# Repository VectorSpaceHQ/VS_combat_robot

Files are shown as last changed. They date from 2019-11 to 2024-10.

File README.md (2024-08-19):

This is an open source, low cost, DIY combat robot kit. It is designed for use with antweight (1lb) and beetleweight (3lb) combat robots.

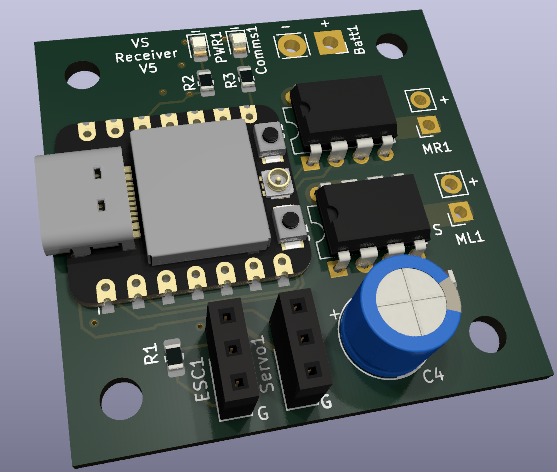
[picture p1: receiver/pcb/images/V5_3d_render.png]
Receiver


This repository includes PCB designs for the transmitter and receiver, the associated software, as well as a simple 3d printable chassis and controller design.

# Troubleshooting

# Invalid head of packet
If the following error occurs when trying to upload to the ESP32, the fix is to hold pin D9 to ground while powering on the board.

A fatal error occurred: Invalid head of packet (0x01): Possible serial noise or corruption.
Failed uploading: uploading error: exit status 2

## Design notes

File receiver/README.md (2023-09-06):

# Hardware
MCU: ESP32-C3
max supply voltage 3.7V

Voltage Regulator: AMS1117-3.3
Max supply voltage 15V. Regulates to 3.3V

Motor Drivers: DRV8873
Vin: 6.5V to 45V
3.6A max

# Software
## Receiver

## Transmitter
### Installation
#### Determine MAC Address of ESP32
1. Upload MAC_finder.ino using Arduino IDE
2. Look at Serial Monitor and copy down resulting MAC address
3. Copy this MAC Address into transmitter.ino

OR

Arduino IDE -> Tools -> Get Board Info

#### Determine joystick rest values

# Troubleshooting
## ESP32 Error: No serial data received

1. Open the Arduino IDE Serial Monitor
2. Hold-down the “BOOT” button
3. Press the “ENABLE” button once
4. Release the finger from the “BOOT” button

## ESP32 Error: A serial exception error occurred: Write timeout
 Press and hold the R button, then press and hold the B button, then release the R button, then release the B button.

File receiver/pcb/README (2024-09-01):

ESP32C3 pin limitations:
https://wiki.seeedstudio.com/exp32c3_d9_d6_d8/

Use D9 only as input
Use D6 only as output but it will sometimes be HIGH, so don't use it for any motors!

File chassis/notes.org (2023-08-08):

* Threaded brass inserts
M3 insert nut needs 4.9mm or 0.19in hole
M4 insert nut needs 5.9mm or 0.23in hole

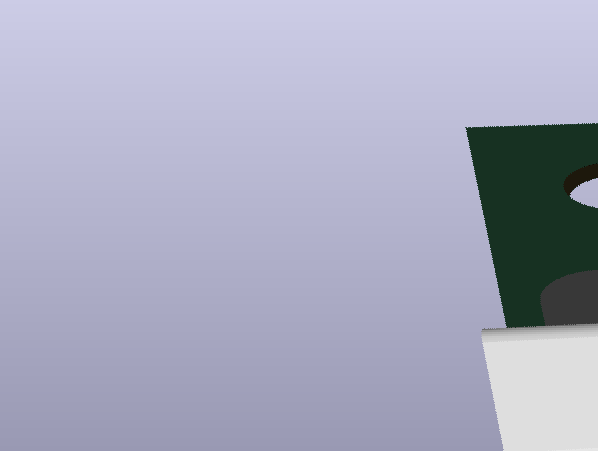
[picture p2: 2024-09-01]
receiver/pcb/images/V6_3d_render.png

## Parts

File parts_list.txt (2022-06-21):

= Robot =
Microcontroller: Arduino Pro Mini 3.3v
Radio: NRF24
Motors: 600 RPM, 12V gear motors
Speed Controller: L298N
Wheels: 75mm foam

= Transmitter =
Microcontroller: Arduino Pro Mini 3.3v
Radio: NRF24

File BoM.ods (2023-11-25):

Item | Quantity | Price Per | Price | Link
Transmitter
PCB | 1 | 1.00 | 1.00
Joysticks | 2 | 1.76 | 3.52 | https://www.digikey.com/en/products/detail/c-k/THB001P/11687191
OLED screen | 1 | 2.00 | 2.00 | https://www.aliexpress.com/item/2251832770994631.html
switches | 2 | 0.70 | 1.40 | https://www.digikey.com/en/products/detail/c-k/JS202011JCQN/6137630
Shoulder buttons | 2 | 0.90 | 1.80 | https://www.digikey.com/en/products/detail/e-switch/PBH4UOANAGX/805274
0805 LED | 1 | 0.30 | 0.30 | https://www.digikey.com/en/products/detail/liteon/LTST-C170KFKT/386775
680 ohm 0805 resistor | 1 | 0.10 | 0.10 | https://www.aliexpress.us/item/3256804579195022.html?curPageLogUid=vwxSfvHASDHL
10Kohm 0805 resistor | 1 | 0.10 | 0.10 | https://www.digikey.com/en/products/detail/stackpole-electronics-inc/RMCF0805JT10K0/1757762
battery clips | 2 | 0.70 | 1.40 | https://www.digikey.com/en/products/detail/keystone-electronics/54/2254090
18650 battery | 1 | 5.00 | 5.00
XIAO ESP32-C3 | 1 | 5.00 | 5.00 | https://www.digikey.com/en/products/detail/seeed-technology-co-ltd/113991054/16652880
 |  | subtotal | 21.62
Receiver
PCB | 1 | 1.00 | 1.00
XT30 connector | 1 | 1.00 | 1.00 | https://www.aliexpress.us/item/2251832360532996.html?curPageLogUid=wmWYOYthzg1A
XIAO ESP32-C3 | 1 | 5.00 | 5.00 | https://www.digikey.com/en/products/detail/seeed-technology-co-ltd/113991054/16652880
9650 buzzer | 1 | 1.80 | 1.80 | https://www.digikey.com/en/products/detail/pui-audio-inc/SMI-1027-T-5V-R/13165916
Ams1117-3.3 | 1 | 0.50 | 0.50 | https://www.digikey.com/en/products/detail/umw/AMS1117-3-3/17635254
L7806 | 1 | 1.17 | 1.17 | https://www.digikey.com/en/products/detail/stmicroelectronics/L7806CD2T-TR/1038242
DRV8870 Hbridge | 2 | 2.20 | 4.40 | https://www.digikey.com/en/products/detail/texas-instruments/DRV8870DDAR/5428828
0.1uF 0805 capacitors | 2 | 0.10 | 0.20 | https://www.digikey.com/en/products/detail/yageo/CC0805KRX7R9BB104/302874
47uF 0805 capacitors | 2 | 1.00 | 2.00 | https://www.aliexpress.us/item/3256802100554482.html?curPageLogUid=Q0m0J4WVnZqB
10 Kohm 0805 resistor | 1 | 0.10 | 0.10 | https://www.digikey.com/en/products/detail/stackpole-electronics-inc/RMCF0805JT10K0/1757762
680 ohm 0805 resistor | 1 | 0.10 | 0.10 | https://www.aliexpress.us/item/3256804579195022.html?curPageLogUid=vwxSfvHASDHL
0805 LED | 1 | 0.30 | 0.30 | https://www.digikey.com/en/products/detail/liteon/LTST-C170KFKT/386775
3 pin male header | 2 | 0.40 | 0.80 | https://www.aliexpress.us/item/2255799947487938.html?curPageLogUid=STjmu7Jf5aUo
 |  | subtotal | 18.37
Chassis
Filament | 1 | 20 | 20
GA25-370 drive motors, 600 RPM | 2 | 10 | 20
tires (Smooth-on Rebound 40) | 1 | 40 | 40
weapon motor | 1 | 20 | 20 | https://www.amazon.com/gp/product/B089YCTT4Y/ref=ppx_yo_dt_b_search_asin_title?ie=UTF8&th=1
brushless ESC 30A | 1 | 18 | 18 | https://www.amazon.com/RC-Brushless-Electric-Controller-bullet/dp/B071GRSFBD
LiPo battery | 1 | 15 | 15 | https://www.amazon.com/Battery-Quadcopter-Helicopter-Airplane-Multi-Motor/dp/B081N9DPVX?s=toys-and-games
On/Off switch | 1 | 10 | 10 | https://www.fingertechrobotics.com/proddetail.php?prod=ft-mini-switch
 |  | subtotal | 143
 |  | Total | 182.99

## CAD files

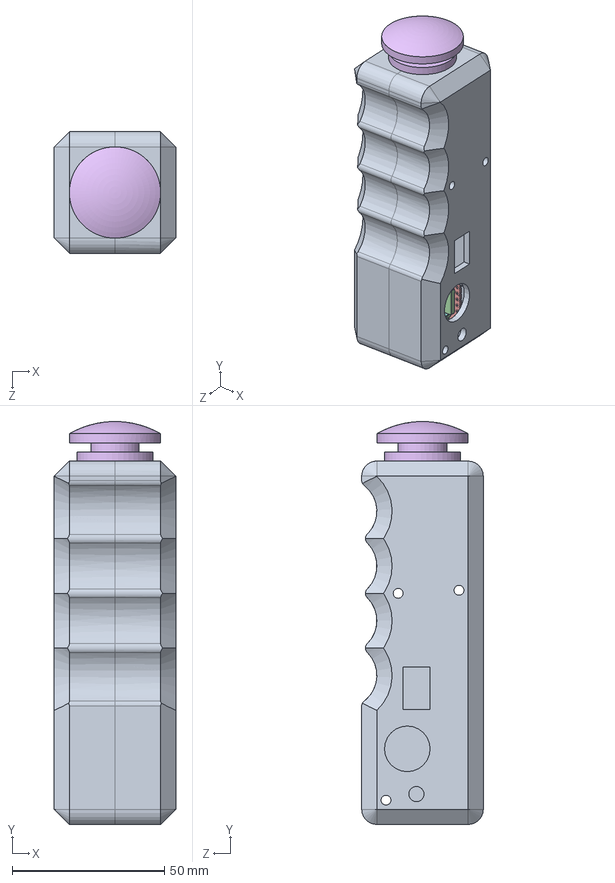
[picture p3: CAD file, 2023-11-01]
arena/cad/ButtonCase.SLDASM
40.0 x 132.5 x 40.0 mm
ButtonCase
BOSS-EXTRUDE14_8_.step
BOSS-EXTRUDE7_4_.step
BOSS-EXTRUDE7_3_.step
BOSS-EXTRUDE14_4_.step
BOSS-EXTRUDE14_2_.step
BOSS-EXTRUDE14_11_.step
BOSS-EXTRUDE7_7_.step
BOSS-EXTRUDE14_9_.step
BOSS-EXTRUDE14_3_.step
BOSS-EXTRUDE14_7_.step
MIRROR2.step
BOSS-EXTRUDE14_5_.step
BOSS-EXTRUDE14_12_.step
BOSS-EXTRUDE7_8_.step
BOSS-EXTRUDE7_1_.step
BOSS-EXTRUDE14_10_.step
BOSS-EXTRUDE7_9_.step
BOSS-EXTRUDE14_6_.step
CHAMFER9.step
BOSS-EXTRUDE14_1_.step
BOSS-EXTRUDE7_6_.step
BOSS-EXTRUDE7_2_.step
CUT-EXTRUDE5.step
BOSS-EXTRUDE7_5_.step
U.FL Connector v1.step
Button (1).step x 2
Shield.step
Seeed Studio XIAO-ESP32-C3.step
TopButton

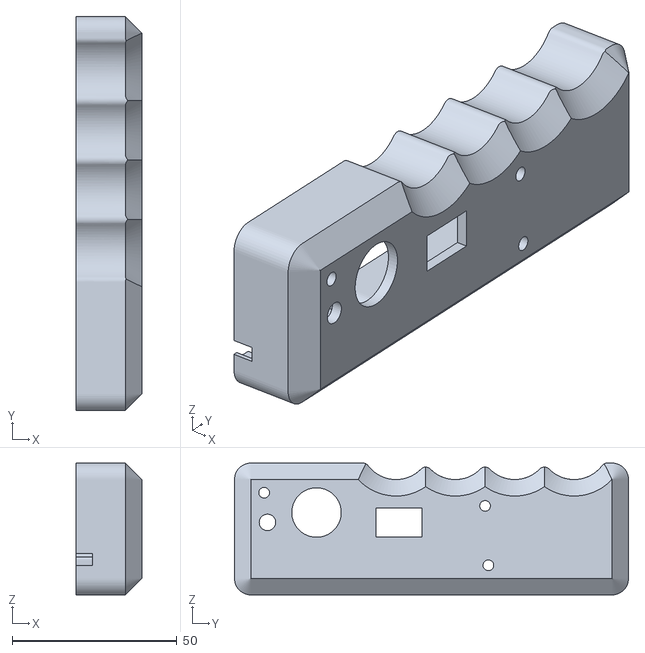
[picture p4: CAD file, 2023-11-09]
arena/cad/ButtonCase-HoleSide.STL
20.0 x 119.5 x 40.0

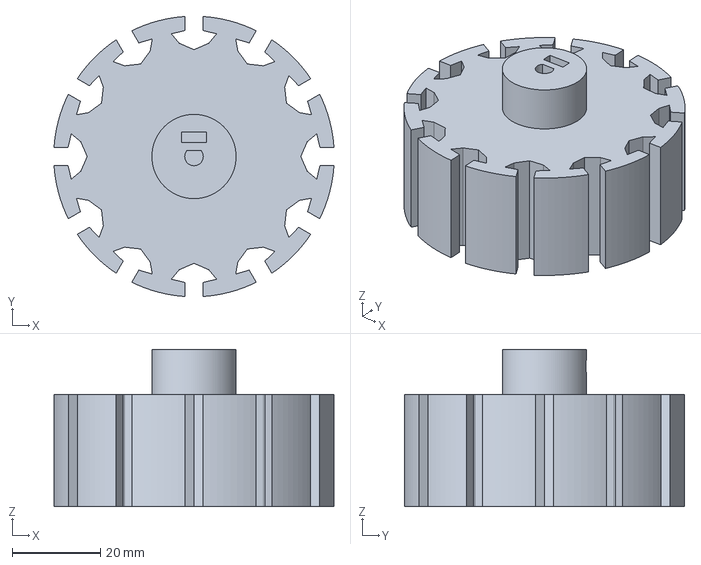
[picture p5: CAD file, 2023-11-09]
chassis/3mf/wheel_hub_casting-wheel.3mf
63.4 x 63.4 x 35.6 mm

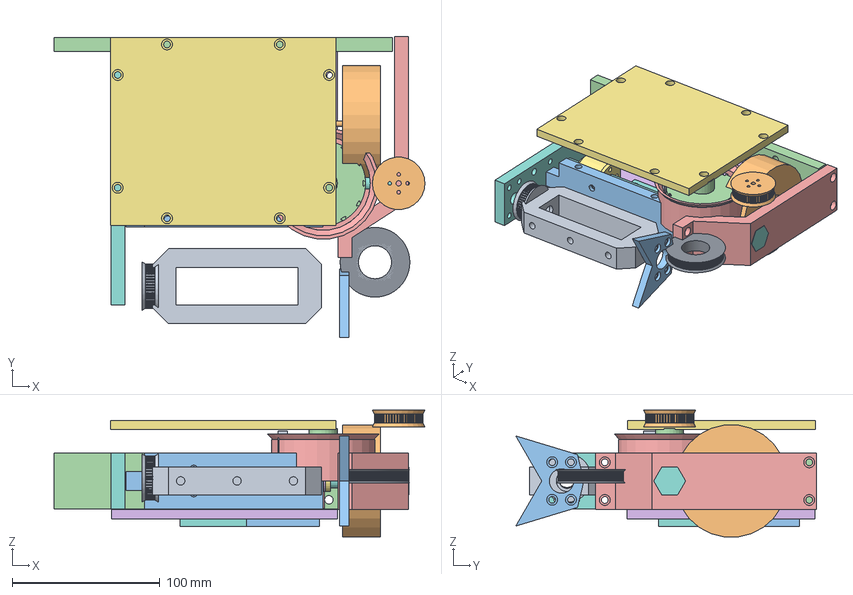
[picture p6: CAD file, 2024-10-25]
chassis/VS_beater_bot/VS_beater_bot.FCStd
250.7 x 203.1 x 85.8 mm
beater-bar
tire
front-plate
rear-plate
wheel-guard
bottom-plate
top-cover
receiver
brushless_motor_mount
drive-motor
battery001
ESC
motor-mount-bottom
motor-mount-top
brushless-motor
beater-shaft
driven-pulley
drive-pulley001
wedge
wheel
tire-mold
spacer-small
spacer-big
right-wall
beater_bar_driven_pulley001 (Solid)

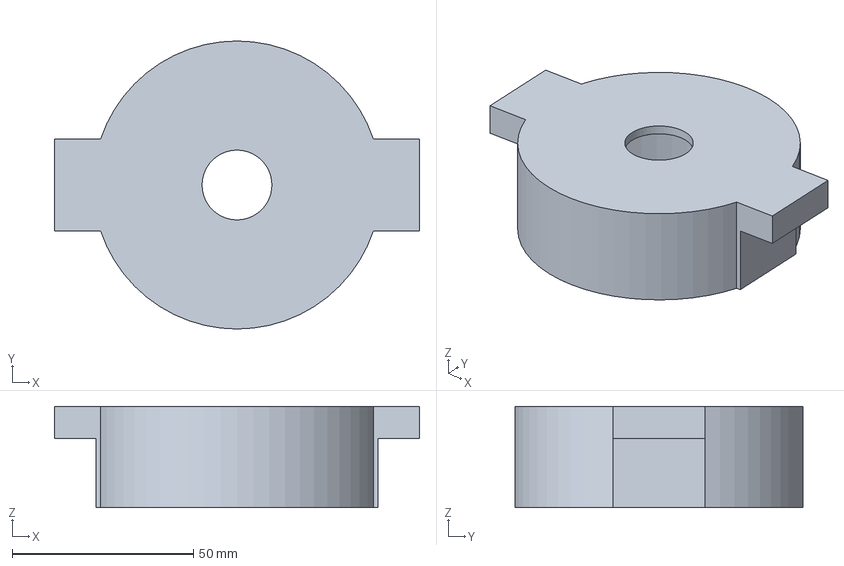
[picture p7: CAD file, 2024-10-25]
chassis/wheel_hub_casting.FCStd
100.6 x 79.4 x 27.9 mm

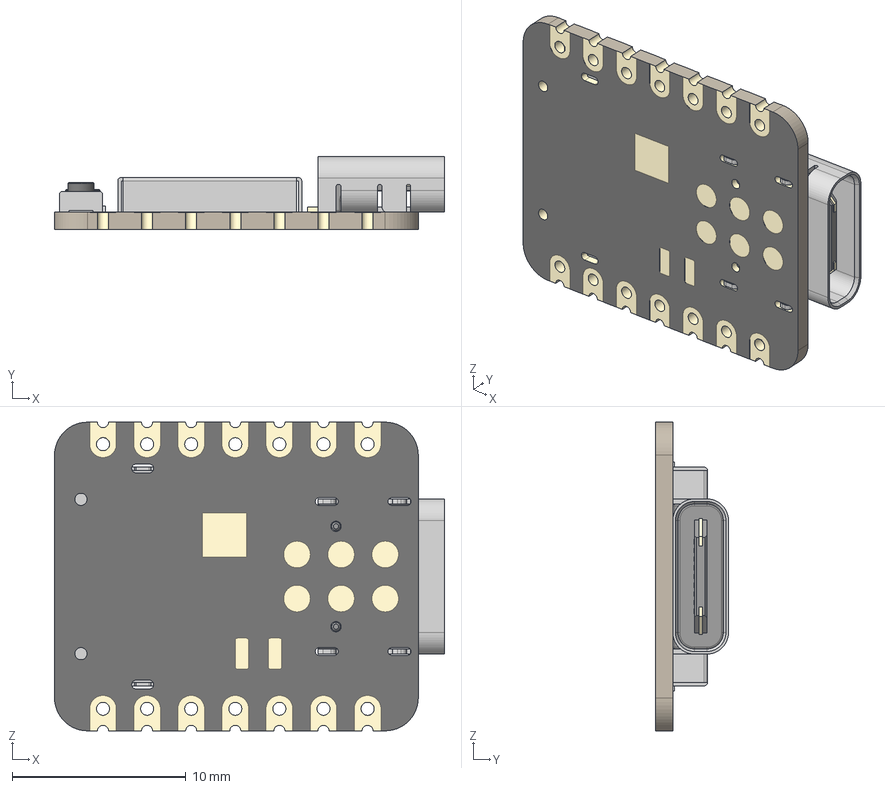
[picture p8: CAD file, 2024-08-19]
receiver/pcb/footprints_and_symbols/XIAO_ESP32C3/Seeed Studio XIAO-ESP32-C3.step
22.5 x 4.21 x 17.8 mm
BOSS-EXTRUDE14_8_
BOSS-EXTRUDE7_4_
BOSS-EXTRUDE7_3_
BOSS-EXTRUDE14_4_
BOSS-EXTRUDE14_2_
BOSS-EXTRUDE14_11_
BOSS-EXTRUDE7_7_
BOSS-EXTRUDE14_9_
BOSS-EXTRUDE14_3_
BOSS-EXTRUDE14_7_
MIRROR2
BOSS-EXTRUDE14_5_
BOSS-EXTRUDE14_12_
BOSS-EXTRUDE7_8_
BOSS-EXTRUDE7_1_
BOSS-EXTRUDE14_10_
BOSS-EXTRUDE7_9_
BOSS-EXTRUDE14_6_
BOSS-EXTRUDE14_1_
BOSS-EXTRUDE7_6_
BOSS-EXTRUDE7_2_
CUT-EXTRUDE5
BOSS-EXTRUDE7_5_
U.FL Connector v1
Button (1) x 2
Shield

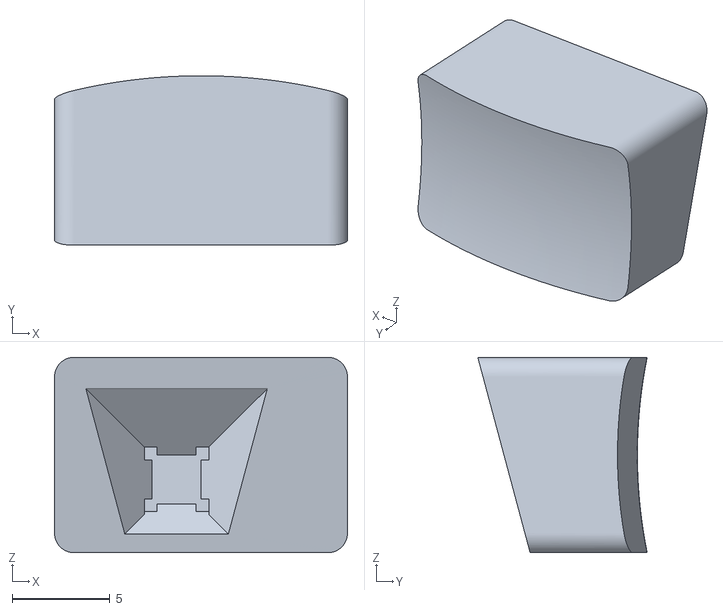
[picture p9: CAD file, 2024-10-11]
transmitter/cad/left trigger button.STL
15.0 x 8.67 x 10.0

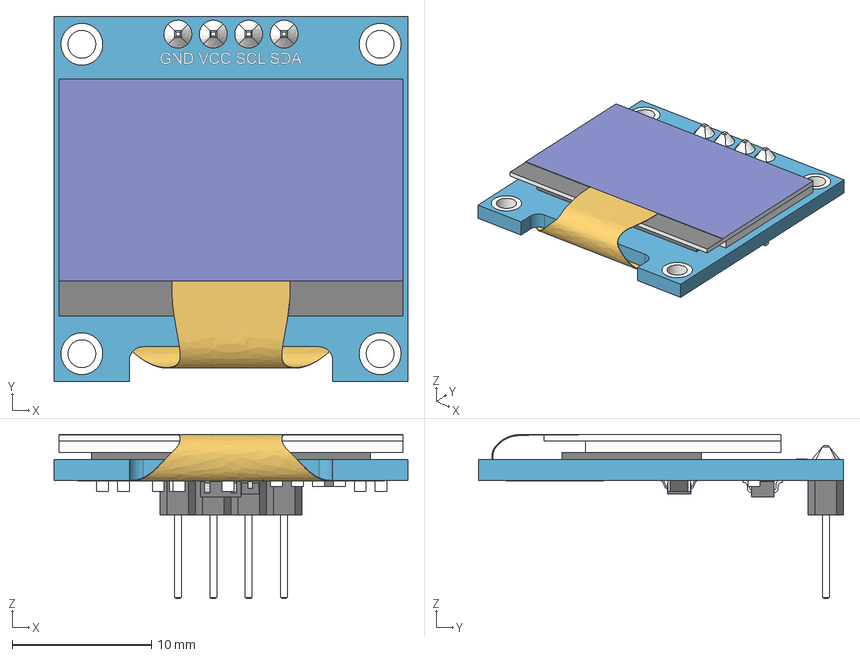
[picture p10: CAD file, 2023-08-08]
transmitter/pcb/component models/SSD1306_OLED_Display(128x64).step
25.4 x 26.2 x 11.8 mm
board
screen
pin_header
soldering
smd_capacitor
smd_capacitor (1)
914_smd_resistor
472_smd_resistor x 3
t4_smd_diode
smd_capacitor (2)
smd_capacitor (3)
smd_capacitor (4)
smd_capacitor (5)
smd_capacitor (6)
472_smd_resistor (1)
SOT-23_XC6206 v3
smd_capacitor (7)
flat_cable

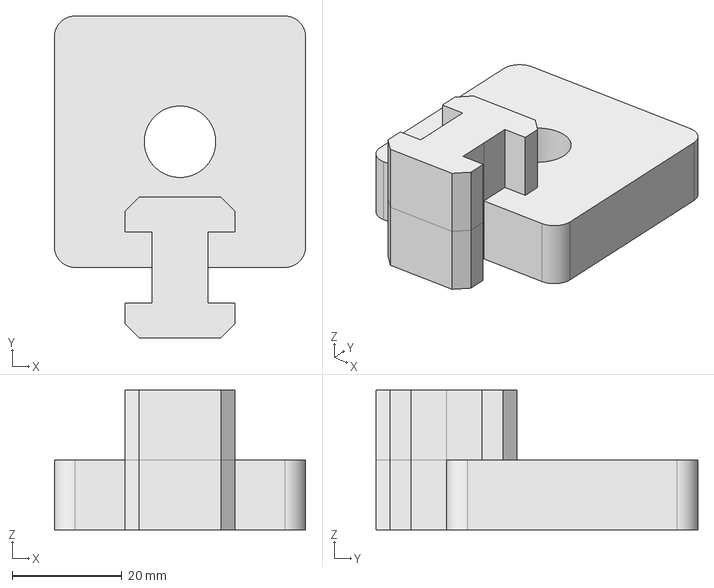
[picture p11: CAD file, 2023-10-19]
arena/t-nuts.FCStd
45.7 x 58.5 x 25.4 mm

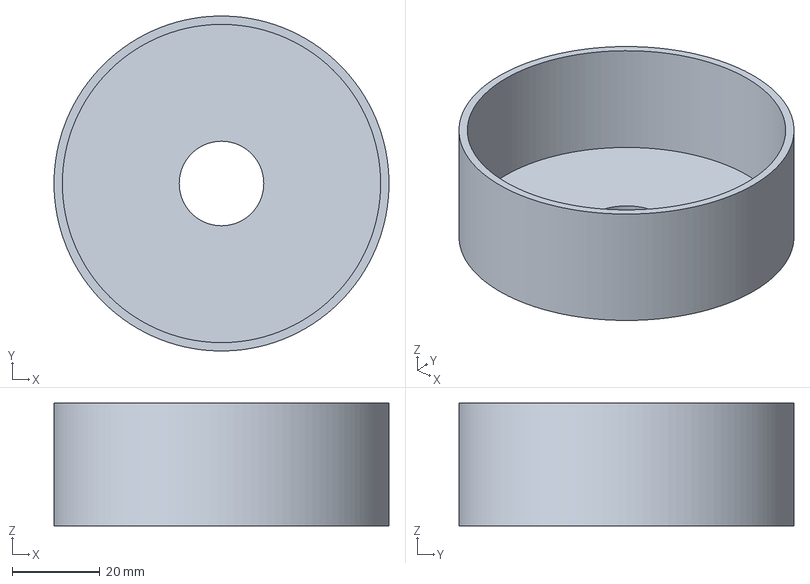
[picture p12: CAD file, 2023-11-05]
chassis/3mf/wheel_hub_casting-mold.3mf
76.2 x 76.2 x 27.9 mm

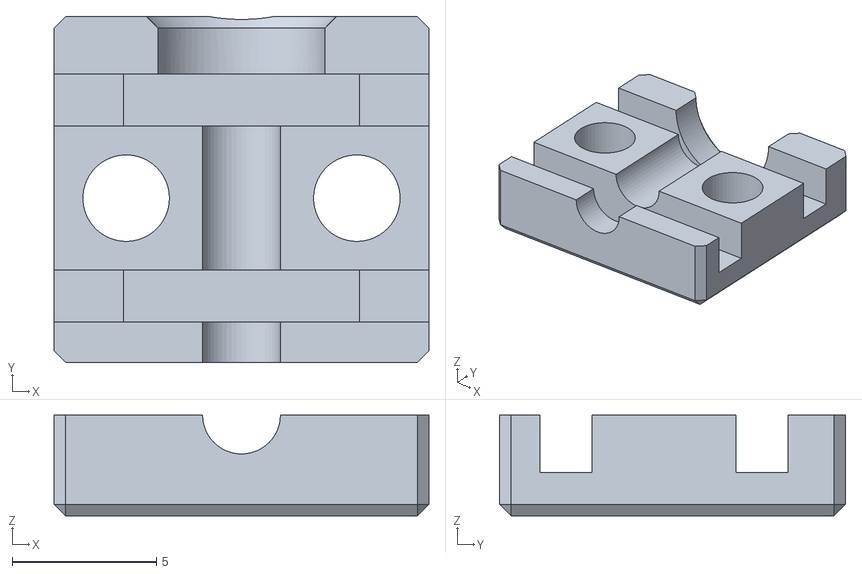
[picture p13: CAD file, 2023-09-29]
chassis/power_switch_half.STL
13.0 x 12.0 x 3.50

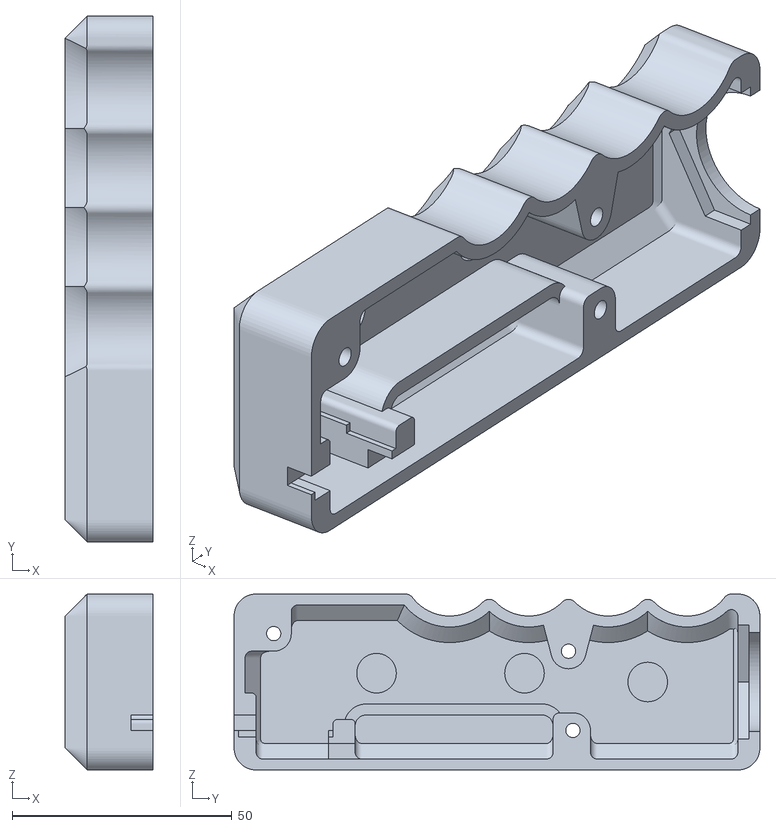
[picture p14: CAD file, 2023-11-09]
arena/cad/ButtonCase-SolidSide.STL
20.0 x 119.5 x 40.0

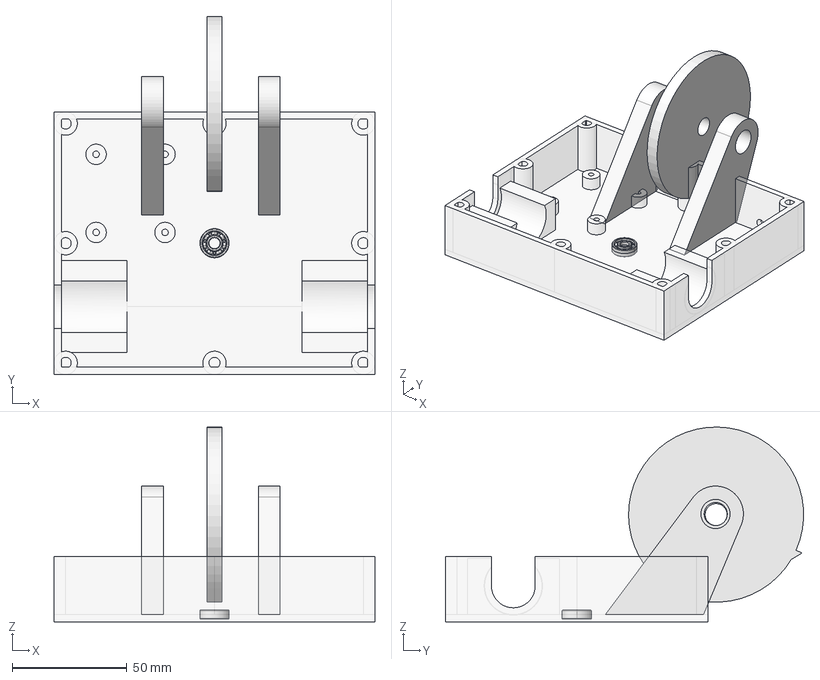
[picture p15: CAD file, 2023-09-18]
chassis/Isaac_combat_robot.FCStd
139.7 x 155.8 x 84.8 mm
main_body
wmount
wmountl
60355K132_Ball Bearing

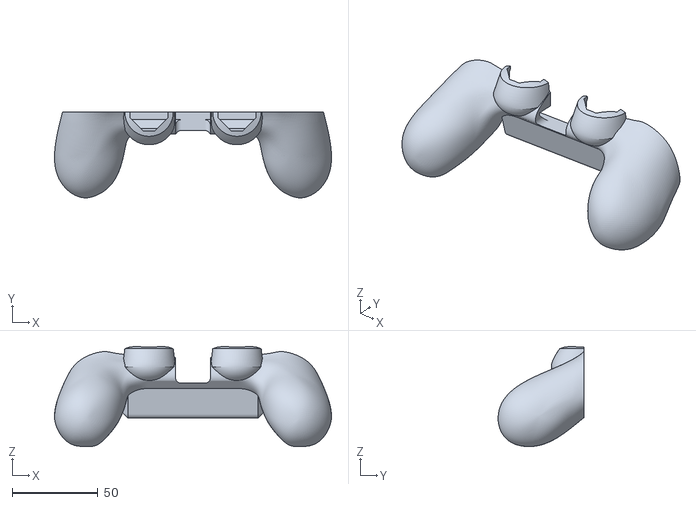
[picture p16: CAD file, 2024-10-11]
transmitter/cad/controller handles.STL
162.0 x 50.2 x 58.6

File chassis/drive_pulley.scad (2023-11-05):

// Parametric Pulley with multiple belt profiles
// by droftarts January 2012

// Based on pulleys by:
// http://www.thingiverse.com/thing:11256 by me!
// https://github.com/prusajr/PrusaMendel by Josef Prusa
// http://www.thingiverse.com/thing:3104 by GilesBathgate
// http://www.thingiverse.com/thing:2079 by nophead

// dxf tooth data from http://oem.cadregister.com/asp/PPOW_Entry.asp?company=915217&elementID=07807803/METRIC/URETH/WV0025/F
// pulley diameter checked and modelled from data at http://www.sdp-si.com/D265/HTML/D265T016.html

/**
 * @name Pulley
 * @category Printed
 * @using 1 x m3 nut, normal or nyloc
 * @using 1 x m3x10 set screw or 1 x m3x8 grub screw
 */


// tuneable constants

teeth = 40;			// Number of teeth, standard Mendel T5 belt = 8, gives Outside Diameter of 11.88mm
profile = 12;		// 1=MXL 2=40DP 3=XL 4=H 5=T2.5 6=T5 7=T10 8=AT5 9=HTD_3mm 10=HTD_5mm 11=HTD_8mm 12=GT2_2mm 13=GT2_3mm 14=GT2_5mm

motor_shaft = 3.5;	// NEMA17 motor shaft exact diameter = 5
m3_dia = 3.2;		// 3mm hole diameter
m3_nut_hex = 1;		// 1 for hex, 0 for square nut
m3_nut_flats = 5.7;	// normal M3 hex nut exact width = 5.5
m3_nut_depth = 2.7;	// normal M3 hex nut exact depth = 2.4, nyloc = 4

retainer = 1;		// Belt retainer above teeth, 0 = No, 1 = Yes
retainer_ht = 1.5;	// height of retainer flange over pulley, standard = 1.5
idler = 1;			// Belt retainer below teeth, 0 = No, 1 = Yes
idler_ht = 1.5;		// height of idler flange over pulley, standard = 1.5

pulley_t_ht = 6.3;	// length of toothed part of pulley, standard = 12
pulley_b_ht = 0;		// pulley base height, standard = 8. Set to same as idler_ht if you want an idler but no pulley.
pulley_b_dia = 20;	// pulley base diameter, standard = 20
no_of_nuts = 1;		// number of captive nuts required, standard = 1
nut_angle = 90;		// angle between nuts, standard = 90
nut_shaft_distance = 1.2;	// distance between inner face of nut and shaft, can be negative.


//	********************************
//	** Scaling tooth for good fit **
//	********************************
/*	To improve fit of belt to pulley, set the following constant. Decrease or increase by 0.1mm at a time. We are modelling the *BELT* tooth here, not the tooth on the pulley. Increasing the number will *decrease* the pulley tooth size. Increasing the tooth width will also scale proportionately the tooth depth, to maintain the shape of the tooth, and increase how far into the pulley the tooth is indented. Can be negative */

additional_tooth_width = 0.2; //mm

//	If you need more tooth depth than this provides, adjust the following constant. However, this will cause the shape of the tooth to change.

additional_tooth_depth = 0; //mm

// calculated constants

nut_elevation = pulley_b_ht/2;
m3_nut_points = 2*((m3_nut_flats/2)/cos(30)); // This is needed for the nut trap

// The following set the pulley diameter for a given number of teeth

MXL_pulley_dia = tooth_spacing (2.032,0.254);
40DP_pulley_dia = tooth_spacing (2.07264,0.1778);
XL_pulley_dia = tooth_spacing (5.08,0.254);
H_pulley_dia = tooth_spacing (9.525,0.381);
T2_5_pulley_dia = tooth_spaceing_curvefit (0.7467,0.796,1.026);
T5_pulley_dia = tooth_spaceing_curvefit (0.6523,1.591,1.064);
T10_pulley_dia = tooth_spacing (10,0.93);
AT5_pulley_dia = tooth_spaceing_curvefit (0.6523,1.591,1.064);
HTD_3mm_pulley_dia = tooth_spacing (3,0.381);
HTD_5mm_pulley_dia = tooth_spacing (5,0.5715);
HTD_8mm_pulley_dia = tooth_spacing (8,0.6858);
GT2_2mm_pulley_dia = tooth_spacing (2,0.254);
GT2_3mm_pulley_dia = tooth_spacing (3,0.381);
GT2_5mm_pulley_dia = tooth_spacing (5,0.5715);

// The following calls the pulley creation part, and passes the pulley diameter and tooth width to that module

if ( profile == 1 ) { pulley ( "MXL" , MXL_pulley_dia , 0.508 , 1.321 ); }
if ( profile == 2 ) { pulley ( "40 D.P." , 40DP_pulley_dia , 0.457 , 1.226 ); }
if ( profile == 3 ) { pulley ( "XL" , XL_pulley_dia , 1.27, 3.051 ); }
if ( profile == 4 ) { pulley ( "H" , H_pulley_dia ,1.905 , 5.359 ); }
if ( profile == 5 ) { pulley ( "T2.5" , T2_5_pulley_dia , 0.7 , 1.678 ); }
if ( profile == 6 ) { pulley ( "T5" , T5_pulley_dia , 1.19 , 3.264 ); }
if ( profile == 7 ) { pulley ( "T10" , T10_pulley_dia , 2.5 , 6.13 ); }
if ( profile == 8 ) { pulley ( "AT5" , AT5_pulley_dia , 1.19 , 4.268 ); }
if ( profile == 9 ) { pulley ( "HTD 3mm" , HTD_3mm_pulley_dia , 1.289 , 2.27 ); }
if ( profile == 10 ) { pulley ( "HTD 5mm" , HTD_5mm_pulley_dia , 2.199 , 3.781 ); }
if ( profile == 11 ) { pulley ( "HTD 8mm" , HTD_8mm_pulley_dia , 3.607 , 6.603 ); }
if ( profile == 12 ) { pulley ( "GT2 2mm" , GT2_2mm_pulley_dia , 0.764 , 1.494 ); }
if ( profile == 13 ) { pulley ( "GT2 3mm" , GT2_3mm_pulley_dia , 1.169 , 2.31 ); }
if ( profile == 14 ) { pulley ( "GT2 5mm" , GT2_5mm_pulley_dia , 1.969 , 3.952 ); }

// Functions

function tooth_spaceing_curvefit (b,c,d)
	= ((c * pow(teeth,d)) / (b + pow(teeth,d))) * teeth ;

function tooth_spacing(tooth_pitch,pitch_line_offset)
	= (2*((teeth*tooth_pitch)/(3.14159265*2)-pitch_line_offset)) ;

// Main Module

module pulley( belt_type , pulley_OD , tooth_depth , tooth_width )
	{
	echo (str("Belt type = ",belt_type,"; Number of teeth = ",teeth,"; Pulley Outside Diameter = ",pulley_OD,"mm "));
	tooth_distance_from_centre = sqrt( pow(pulley_OD/2,2) - pow((tooth_width+additional_tooth_width)/2,2));
	tooth_width_scale = (tooth_width + additional_tooth_width ) / tooth_width;
	tooth_depth_scale = ((tooth_depth + additional_tooth_depth ) / tooth_depth) ;


//	************************************************************************
//	*** uncomment the following line if pulley is wider than puller base ***
//	************************************************************************

//	translate ([0,0, pulley_b_ht + pulley_t_ht + retainer_ht ]) rotate ([0,180,0])

	difference()
	 {	 
		union()
		{
			//base
	
			if ( pulley_b_ht < 2 ) { echo ("CAN'T DRAW PULLEY BASE, HEIGHT LESS THAN 2!!!"); } else {
				rotate_extrude($fn=pulley_b_dia*2)
				{
						square([pulley_b_dia/2-1,pulley_b_ht]);
						square([pulley_b_dia/2,pulley_b_ht-1]);
						translate([pulley_b_dia/2-1,pulley_b_ht-1]) circle(1);
				}
			}
	
		difference()
			{
			//shaft - diameter is outside diameter of pulley
			
			translate([0,0,pulley_b_ht]) 
			rotate ([0,0,360/(teeth*4)]) 
			cylinder(r=pulley_OD/2,h=pulley_t_ht, $fn=teeth*4);
	
			//teeth - cut out of shaft
		
			for(i=[1:teeth]) 
			rotate([0,0,i*(360/teeth)])
			translate([0,-tooth_distance_from_centre,pulley_b_ht -1]) 
			scale ([ tooth_width_scale , tooth_depth_scale , 1 ]) 
			{
			if ( profile == 1 ) { MXL();}
			if ( profile == 2 ) { 40DP();}
			if ( profile == 3 ) { XL();}
			if ( profile == 4 ) { H();}
			if ( profile == 5 ) { T2_5();}
			if ( profile == 6 ) { T5();}
			if ( profile == 7 ) { T10();}
			if ( profile == 8 ) { AT5();}
			if ( profile == 9 ) { HTD_3mm();}
			if ( profile == 10 ) { HTD_5mm();}
			if ( profile == 11 ) { HTD_8mm();}
			if ( profile == 12 ) { GT2_2mm();}
			if ( profile == 13 ) { GT2_3mm();}
			if ( profile == 14 ) { GT2_5mm();}
			}

			}
			
		//belt retainer / idler
		if ( retainer > 0 ) {translate ([0,0, pulley_b_ht + pulley_t_ht ]) 
		rotate_extrude($fn=teeth*4)  
		polygon([[0,0],[pulley_OD/2,0],[pulley_OD/2 + retainer_ht , retainer_ht],[0 , retainer_ht],[0,0]]);}
		
		if ( idler > 0 ) {translate ([0,0, pulley_b_ht - idler_ht ]) 
		rotate_extrude($fn=teeth*4)  
		polygon([[0,0],[pulley_OD/2 + idler_ht,0],[pulley_OD/2 , idler_ht],[0 , idler_ht],[0,0]]);}
	
		}
	   
		//hole for motor shaft
		translate([0,0,-1])cylinder(r=motor_shaft/2,h=pulley_b_ht + pulley_t_ht + retainer_ht + 2,$fn=motor_shaft*4);
				
		//captive nut and grub screw holes
	
		if ( pulley_b_ht < m3_nut_flats ) { echo ("CAN'T DRAW CAPTIVE NUTS, HEIGHT LESS THAN NUT DIAMETER!!!"); } else {
		if ( (pulley_b_dia - motor_shaft)/2 < m3_nut_depth + 3 ) { echo ("CAN'T DRAW CAPTIVE NUTS, DIAMETER TOO SMALL FOR NUT DEPTH!!!"); } else {
	
			for(j=[1:no_of_nuts]) rotate([0,0,j*nut_angle])
			translate([0,0,nut_elevation])rotate([90,0,0])
	
			union()
			{
				//entrance
				translate([0,-pulley_b_ht/4-0.5,motor_shaft/2+m3_nut_depth/2+nut_shaft_distance]) cube([m3_nut_flats,pulley_b_ht/2+1,m3_nut_depth],center=true);
	
				//nut
				if ( m3_nut_hex > 0 )
					{
						// hex nut
						translate([0,0.25,motor_shaft/2+m3_nut_depth/2+nut_shaft_distance]) rotate([0,0,30]) cylinder(r=m3_nut_points/2,h=m3_nut_depth,center=true,$fn=6);
					} else {
						// square nut
						translate([0,0.25,motor_shaft/2+m3_nut_depth/2+nut_shaft_distance]) cube([m3_nut_flats,m3_nut_flats,m3_nut_depth],center=true);
					}
	
				//grub screw hole
				rotate([0,0,22.5])cylinder(r=m3_dia/2,h=pulley_b_dia/2+1,$fn=8);
			}
		}}
	 }
	   
	}


// Tooth profile modules
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

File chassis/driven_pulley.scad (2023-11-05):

// Parametric Pulley with multiple belt profiles
// by droftarts January 2012

// Based on pulleys by:
// http://www.thingiverse.com/thing:11256 by me!
// https://github.com/prusajr/PrusaMendel by Josef Prusa
// http://www.thingiverse.com/thing:3104 by GilesBathgate
// http://www.thingiverse.com/thing:2079 by nophead

// dxf tooth data from http://oem.cadregister.com/asp/PPOW_Entry.asp?company=915217&elementID=07807803/METRIC/URETH/WV0025/F
// pulley diameter checked and modelled from data at http://www.sdp-si.com/D265/HTML/D265T016.html

/**
 * @name Pulley
 * @category Printed
 * @using 1 x m3 nut, normal or nyloc
 * @using 1 x m3x10 set screw or 1 x m3x8 grub screw
 */


// tuneable constants

teeth = 70;			// Number of teeth, standard Mendel T5 belt = 8, gives Outside Diameter of 11.88mm
profile = 12;		// 1=MXL 2=40DP 3=XL 4=H 5=T2.5 6=T5 7=T10 8=AT5 9=HTD_3mm 10=HTD_5mm 11=HTD_8mm 12=GT2_2mm 13=GT2_3mm 14=GT2_5mm

motor_shaft = 22.3;	// NEMA17 motor shaft exact diameter = 5
m3_dia = 3.2;		// 3mm hole diameter
m3_nut_hex = 1;		// 1 for hex, 0 for square nut
m3_nut_flats = 5.7;	// normal M3 hex nut exact width = 5.5
m3_nut_depth = 2.7;	// normal M3 hex nut exact depth = 2.4, nyloc = 4

retainer = 1;		// Belt retainer above teeth, 0 = No, 1 = Yes
retainer_ht = 1.5;	// height of retainer flange over pulley, standard = 1.5
idler = 1;			// Belt retainer below teeth, 0 = No, 1 = Yes
idler_ht = 1.5;		// height of idler flange over pulley, standard = 1.5

pulley_t_ht = 6.3;	// length of toothed part of pulley, standard = 12
pulley_b_ht = 0;		// pulley base height, standard = 8. Set to same as idler_ht if you want an idler but no pulley.
pulley_b_dia = 20;	// pulley base diameter, standard = 20
no_of_nuts = 1;		// number of captive nuts required, standard = 1
nut_angle = 90;		// angle between nuts, standard = 90
nut_shaft_distance = 1.2;	// distance between inner face of nut and shaft, can be negative.


//	********************************
//	** Scaling tooth for good fit **
//	********************************
/*	To improve fit of belt to pulley, set the following constant. Decrease or increase by 0.1mm at a time. We are modelling the *BELT* tooth here, not the tooth on the pulley. Increasing the number will *decrease* the pulley tooth size. Increasing the tooth width will also scale proportionately the tooth depth, to maintain the shape of the tooth, and increase how far into the pulley the tooth is indented. Can be negative */

additional_tooth_width = 0.2; //mm

//	If you need more tooth depth than this provides, adjust the following constant. However, this will cause the shape of the tooth to change.

additional_tooth_depth = 0; //mm

// calculated constants

nut_elevation = pulley_b_ht/2;
m3_nut_points = 2*((m3_nut_flats/2)/cos(30)); // This is needed for the nut trap

// The following set the pulley diameter for a given number of teeth

MXL_pulley_dia = tooth_spacing (2.032,0.254);
40DP_pulley_dia = tooth_spacing (2.07264,0.1778);
XL_pulley_dia = tooth_spacing (5.08,0.254);
H_pulley_dia = tooth_spacing (9.525,0.381);
T2_5_pulley_dia = tooth_spaceing_curvefit (0.7467,0.796,1.026);
T5_pulley_dia = tooth_spaceing_curvefit (0.6523,1.591,1.064);
T10_pulley_dia = tooth_spacing (10,0.93);
AT5_pulley_dia = tooth_spaceing_curvefit (0.6523,1.591,1.064);
HTD_3mm_pulley_dia = tooth_spacing (3,0.381);
HTD_5mm_pulley_dia = tooth_spacing (5,0.5715);
HTD_8mm_pulley_dia = tooth_spacing (8,0.6858);
GT2_2mm_pulley_dia = tooth_spacing (2,0.254);
GT2_3mm_pulley_dia = tooth_spacing (3,0.381);
GT2_5mm_pulley_dia = tooth_spacing (5,0.5715);

// The following calls the pulley creation part, and passes the pulley diameter and tooth width to that module

if ( profile == 1 ) { pulley ( "MXL" , MXL_pulley_dia , 0.508 , 1.321 ); }
if ( profile == 2 ) { pulley ( "40 D.P." , 40DP_pulley_dia , 0.457 , 1.226 ); }
if ( profile == 3 ) { pulley ( "XL" , XL_pulley_dia , 1.27, 3.051 ); }
if ( profile == 4 ) { pulley ( "H" , H_pulley_dia ,1.905 , 5.359 ); }
if ( profile == 5 ) { pulley ( "T2.5" , T2_5_pulley_dia , 0.7 , 1.678 ); }
if ( profile == 6 ) { pulley ( "T5" , T5_pulley_dia , 1.19 , 3.264 ); }
if ( profile == 7 ) { pulley ( "T10" , T10_pulley_dia , 2.5 , 6.13 ); }
if ( profile == 8 ) { pulley ( "AT5" , AT5_pulley_dia , 1.19 , 4.268 ); }
if ( profile == 9 ) { pulley ( "HTD 3mm" , HTD_3mm_pulley_dia , 1.289 , 2.27 ); }
if ( profile == 10 ) { pulley ( "HTD 5mm" , HTD_5mm_pulley_dia , 2.199 , 3.781 ); }
if ( profile == 11 ) { pulley ( "HTD 8mm" , HTD_8mm_pulley_dia , 3.607 , 6.603 ); }
if ( profile == 12 ) { pulley ( "GT2 2mm" , GT2_2mm_pulley_dia , 0.764 , 1.494 ); }
if ( profile == 13 ) { pulley ( "GT2 3mm" , GT2_3mm_pulley_dia , 1.169 , 2.31 ); }
if ( profile == 14 ) { pulley ( "GT2 5mm" , GT2_5mm_pulley_dia , 1.969 , 3.952 ); }

// Functions

function tooth_spaceing_curvefit (b,c,d)
	= ((c * pow(teeth,d)) / (b + pow(teeth,d))) * teeth ;

function tooth_spacing(tooth_pitch,pitch_line_offset)
	= (2*((teeth*tooth_pitch)/(3.14159265*2)-pitch_line_offset)) ;

// Main Module

module pulley( belt_type , pulley_OD , tooth_depth , tooth_width )
	{
	echo (str("Belt type = ",belt_type,"; Number of teeth = ",teeth,"; Pulley Outside Diameter = ",pulley_OD,"mm "));
	tooth_distance_from_centre = sqrt( pow(pulley_OD/2,2) - pow((tooth_width+additional_tooth_width)/2,2));
	tooth_width_scale = (tooth_width + additional_tooth_width ) / tooth_width;
	tooth_depth_scale = ((tooth_depth + additional_tooth_depth ) / tooth_depth) ;


//	************************************************************************
//	*** uncomment the following line if pulley is wider than puller base ***
//	************************************************************************

//	translate ([0,0, pulley_b_ht + pulley_t_ht + retainer_ht ]) rotate ([0,180,0])

	difference()
	 {	 
		union()
		{
			//base
	
			if ( pulley_b_ht < 2 ) { echo ("CAN'T DRAW PULLEY BASE, HEIGHT LESS THAN 2!!!"); } else {
				rotate_extrude($fn=pulley_b_dia*2)
				{
						square([pulley_b_dia/2-1,pulley_b_ht]);
						square([pulley_b_dia/2,pulley_b_ht-1]);
						translate([pulley_b_dia/2-1,pulley_b_ht-1]) circle(1);
				}
			}
	
		difference()
			{
			//shaft - diameter is outside diameter of pulley
			
			translate([0,0,pulley_b_ht]) 
			rotate ([0,0,360/(teeth*4)]) 
			cylinder(r=pulley_OD/2,h=pulley_t_ht, $fn=teeth*4);
	
			//teeth - cut out of shaft
		
			for(i=[1:teeth]) 
			rotate([0,0,i*(360/teeth)])
			translate([0,-tooth_distance_from_centre,pulley_b_ht -1]) 
			scale ([ tooth_width_scale , tooth_depth_scale , 1 ]) 
			{
			if ( profile == 1 ) { MXL();}
			if ( profile == 2 ) { 40DP();}
			if ( profile == 3 ) { XL();}
			if ( profile == 4 ) { H();}
			if ( profile == 5 ) { T2_5();}
			if ( profile == 6 ) { T5();}
			if ( profile == 7 ) { T10();}
			if ( profile == 8 ) { AT5();}
			if ( profile == 9 ) { HTD_3mm();}
			if ( profile == 10 ) { HTD_5mm();}
			if ( profile == 11 ) { HTD_8mm();}
			if ( profile == 12 ) { GT2_2mm();}
			if ( profile == 13 ) { GT2_3mm();}
			if ( profile == 14 ) { GT2_5mm();}
			}

			}
			
		//belt retainer / idler
		if ( retainer > 0 ) {translate ([0,0, pulley_b_ht + pulley_t_ht ]) 
		rotate_extrude($fn=teeth*4)  
		polygon([[0,0],[pulley_OD/2,0],[pulley_OD/2 + retainer_ht , retainer_ht],[0 , retainer_ht],[0,0]]);}
		
		if ( idler > 0 ) {translate ([0,0, pulley_b_ht - idler_ht ]) 
		rotate_extrude($fn=teeth*4)  
		polygon([[0,0],[pulley_OD/2 + idler_ht,0],[pulley_OD/2 , idler_ht],[0 , idler_ht],[0,0]]);}
	
		}
	   
		//hole for motor shaft
		translate([0,0,-4])cylinder(r=motor_shaft/2,h=pulley_b_ht + pulley_t_ht + retainer_ht + 12,$fn=motor_shaft*4);
				
		//captive nut and grub screw holes
	
		if ( pulley_b_ht < m3_nut_flats ) { echo ("CAN'T DRAW CAPTIVE NUTS, HEIGHT LESS THAN NUT DIAMETER!!!"); } else {
		if ( (pulley_b_dia - motor_shaft)/2 < m3_nut_depth + 3 ) { echo ("CAN'T DRAW CAPTIVE NUTS, DIAMETER TOO SMALL FOR NUT DEPTH!!!"); } else {
	
			for(j=[1:no_of_nuts]) rotate([0,0,j*nut_angle])
			translate([0,0,nut_elevation])rotate([90,0,0])
	
			union()
			{
				//entrance
				translate([0,-pulley_b_ht/4-0.5,motor_shaft/2+m3_nut_depth/2+nut_shaft_distance]) cube([m3_nut_flats,pulley_b_ht/2+1,m3_nut_depth],center=true);
	
				//nut
				if ( m3_nut_hex > 0 )
					{
						// hex nut
						translate([0,0.25,motor_shaft/2+m3_nut_depth/2+nut_shaft_distance]) rotate([0,0,30]) cylinder(r=m3_nut_points/2,h=m3_nut_depth,center=true,$fn=6);
					} else {
						// square nut
						translate([0,0.25,motor_shaft/2+m3_nut_depth/2+nut_shaft_distance]) cube([m3_nut_flats,m3_nut_flats,m3_nut_depth],center=true);
					}
	
				//grub screw hole
				rotate([0,0,22.5])cylinder(r=m3_dia/2,h=pulley_b_dia/2+1,$fn=8);
			}
		}}
	 }
	   
	}


// Tooth profile modules
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

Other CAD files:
arena/connection_plates.FCStd
arena/cad/ButtonCase-HoleSide-NoReset.STL
transmitter/cad/right trigger button.STL
transmitter/pcb/component models/Seeed Studio XIAO-ESP32-C3.step
arena/cad/ButtonCase.SLDPRT
arena/cad/TopButton.SLDPRT
chassis/wheel_hub.FCStd
transmitter/cad/controller back.STL
transmitter/cad/controller thumbstick.SLDPRT
transmitter/cad/controller thumbstick.STL
transmitter/cad/controller trigger button.SLDPRT
transmitter/pcb/component models/54.step
transmitter/pcb/component models/JS202011JCQN.step
transmitter/pcb/component models/JS202011SCQN.step
transmitter/pcb/component models/PBH2UEESNPNAGX.step
transmitter/pcb/component models/THB001P.stp

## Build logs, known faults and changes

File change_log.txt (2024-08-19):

== v5
** Use electrolytic capacitor for 470uF
** 3.3v output from UA78M33CDCYRG3 was going to 5V pin of ESP, fixed to 3.3V pin.

== v4
* Receiver
** Replaced Buzzer with LED for diagnostics
** Replaced AMS1117 with UA78M33CDCYRG3 because it rolls off the tongue and handles higher Vin, including 4s LiPo.
** Added more spacing between battery connection pads
** Clearly labeled left and right motors
** Switched from DRV8870 to DRV8851
* Transmitter
* Chassis
** Thickened walls
** Added belt tension
** Added walls around weapon motor to protect wires
** Extended weapon supports to allow weapon to spin when upside down

== v3 PCBs, commit d353bc9  ==
* Complete redesign from scratch.
* Switching from Arduino to ESP32-C3 MCUs
* More integrated design such as directly mounting our own H-bridges.
* Switching from NRF24 to Bluetooth

== Changes from VS v1 to v2 boards ==
* Add better silkscreen guidance on receiver for the NRF24 board and for output pins.

== Changes from Team Panic to VS v1 board ==
* Added on/off switch
* Two joysticks, as one is difficult to mix and control. They're also extremely cheap.
* Joysticks connect to female headers rather than being soldered directly. Easily replacable and easier to install.
* Uses a 3.3V Arduino Pro Mini instead of 5V, making the Arduino the only necessary voltage regulator.
* Voltage regulator goes directly to VCC and VCC ties to NRF24. This allows powering both components through the USB programmer, no longer requiring a battery to be plugged in for testing.
* Added an LED for active communications indication
* Weapon is now an on/off switch
* Receiver has pads for the motor control signals

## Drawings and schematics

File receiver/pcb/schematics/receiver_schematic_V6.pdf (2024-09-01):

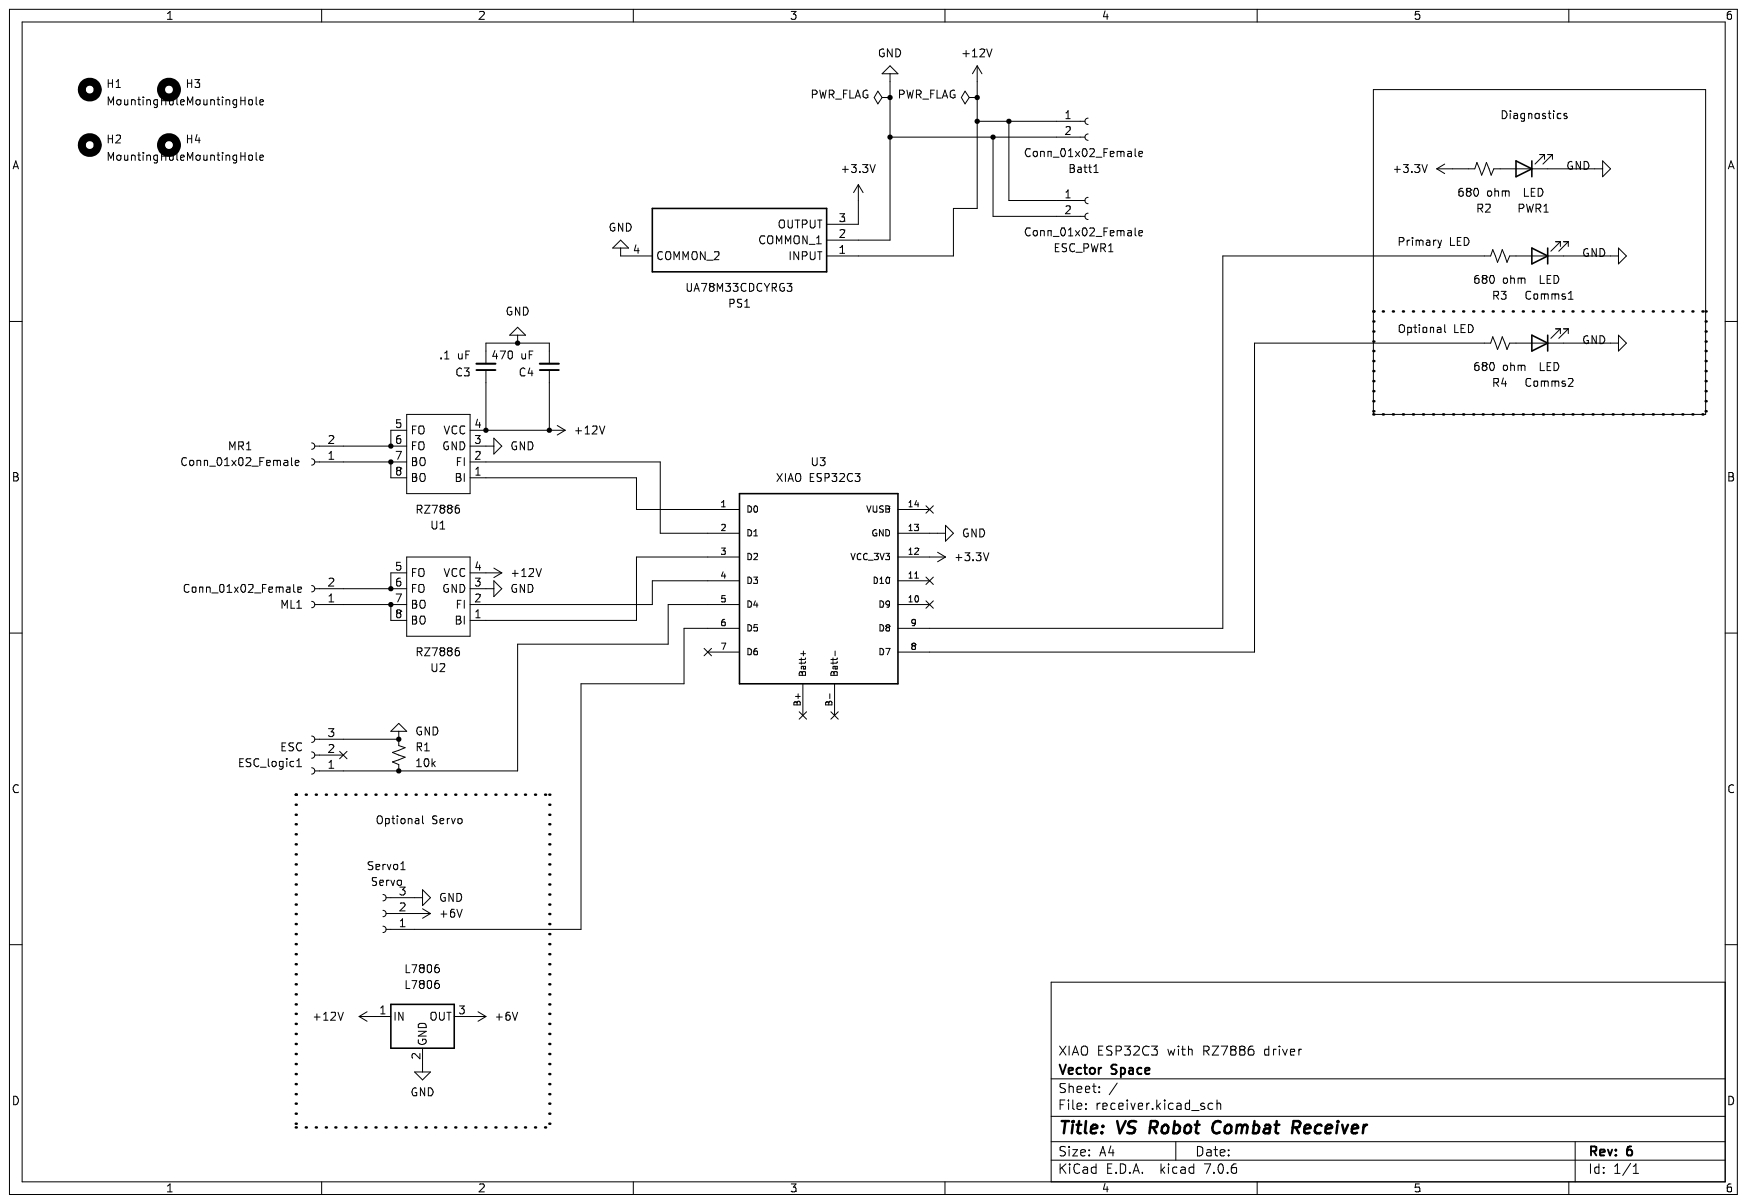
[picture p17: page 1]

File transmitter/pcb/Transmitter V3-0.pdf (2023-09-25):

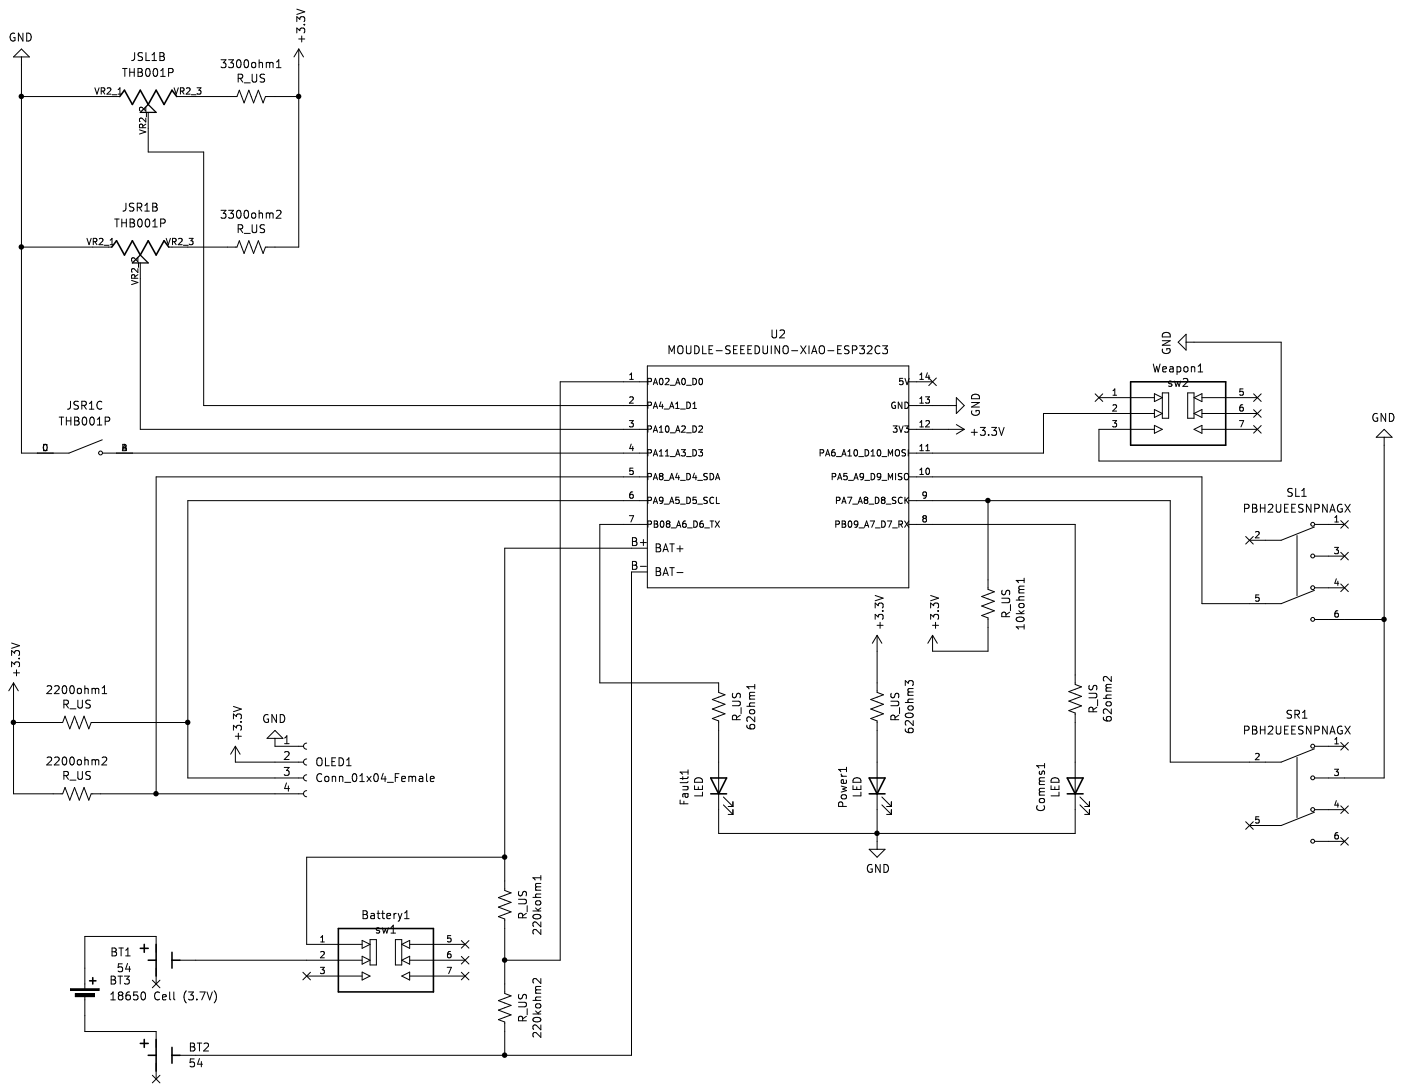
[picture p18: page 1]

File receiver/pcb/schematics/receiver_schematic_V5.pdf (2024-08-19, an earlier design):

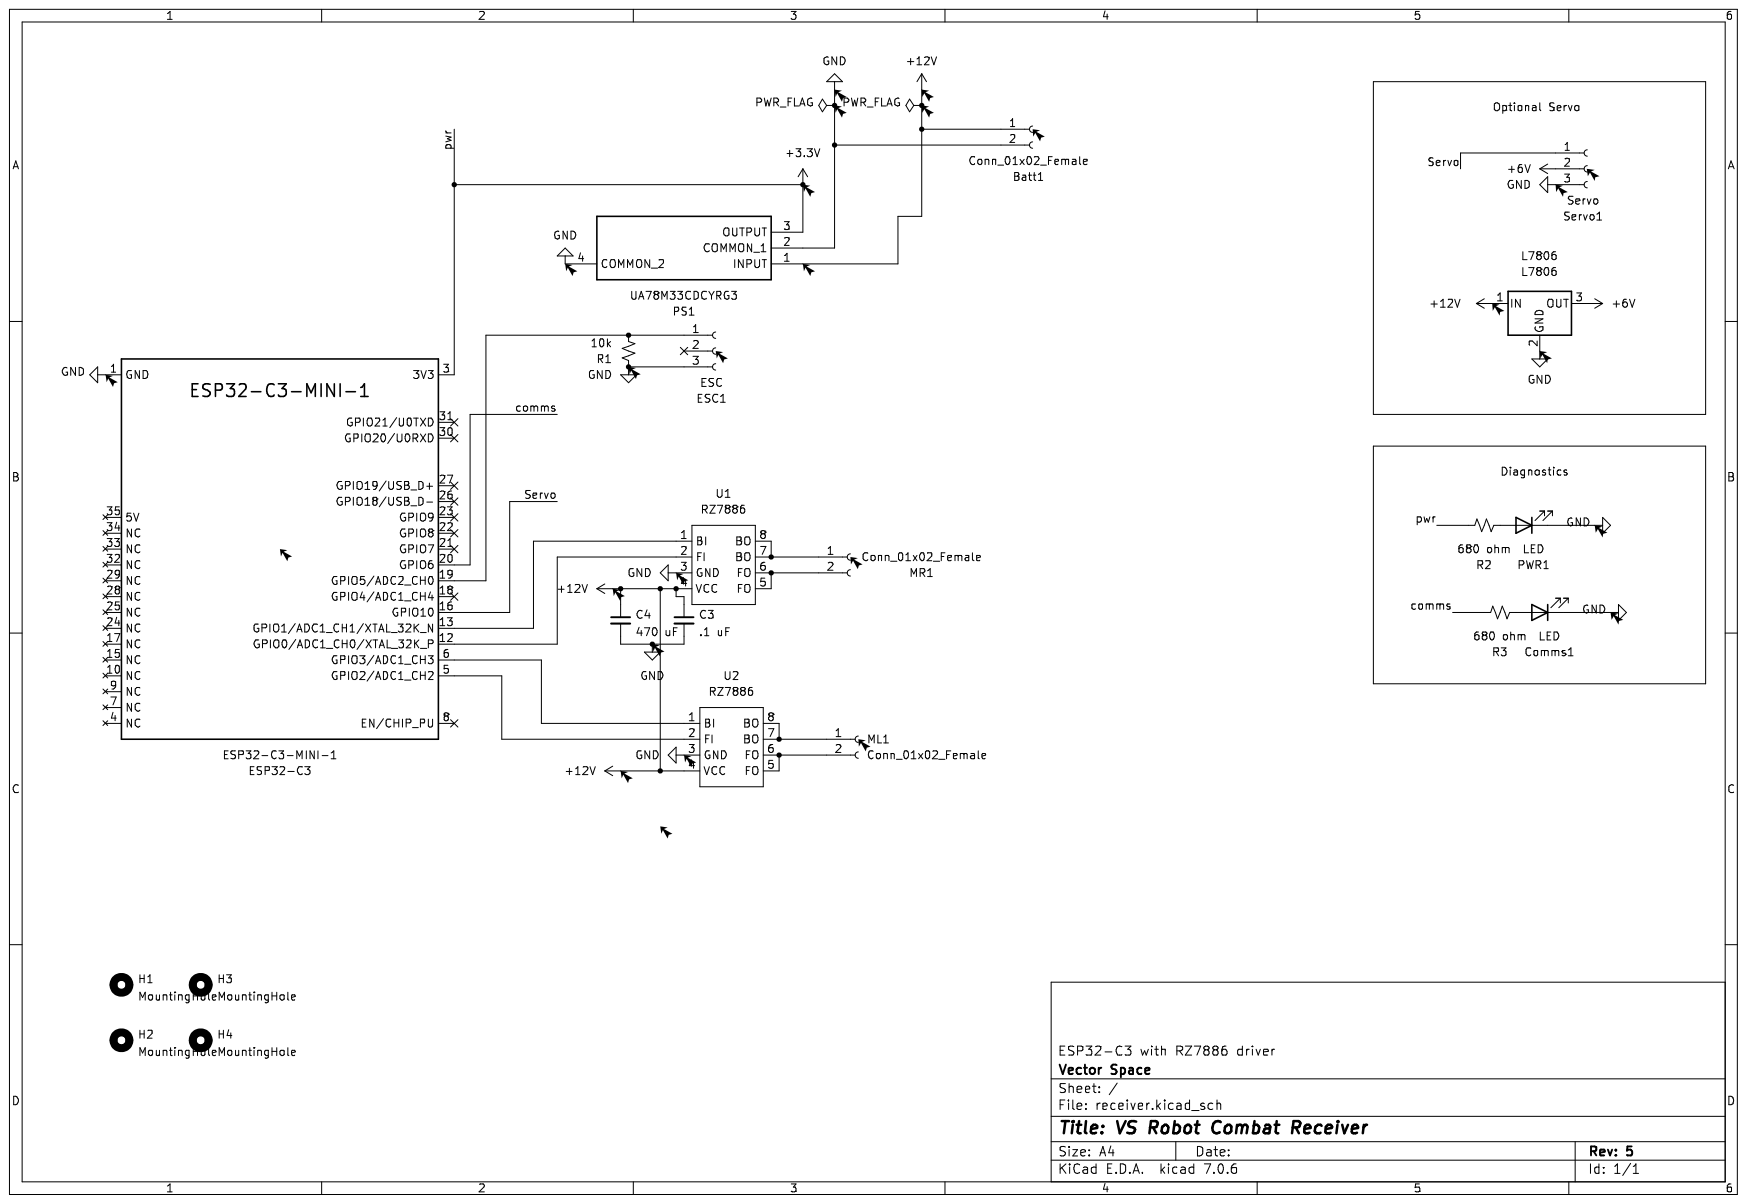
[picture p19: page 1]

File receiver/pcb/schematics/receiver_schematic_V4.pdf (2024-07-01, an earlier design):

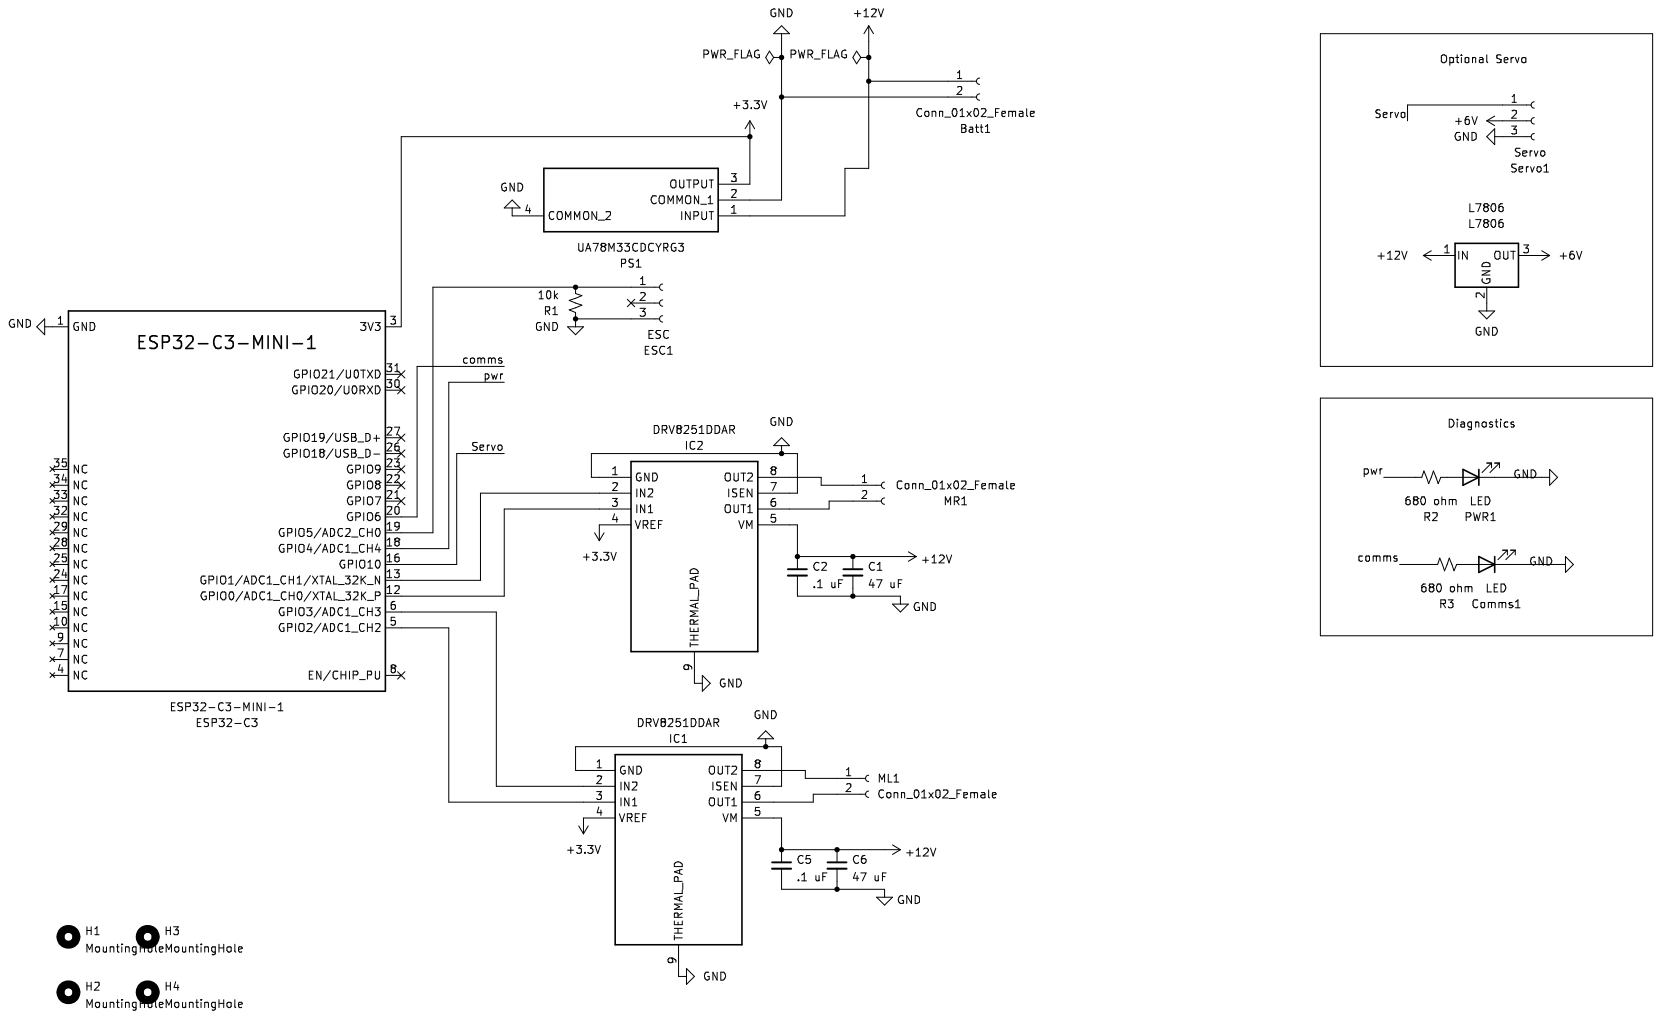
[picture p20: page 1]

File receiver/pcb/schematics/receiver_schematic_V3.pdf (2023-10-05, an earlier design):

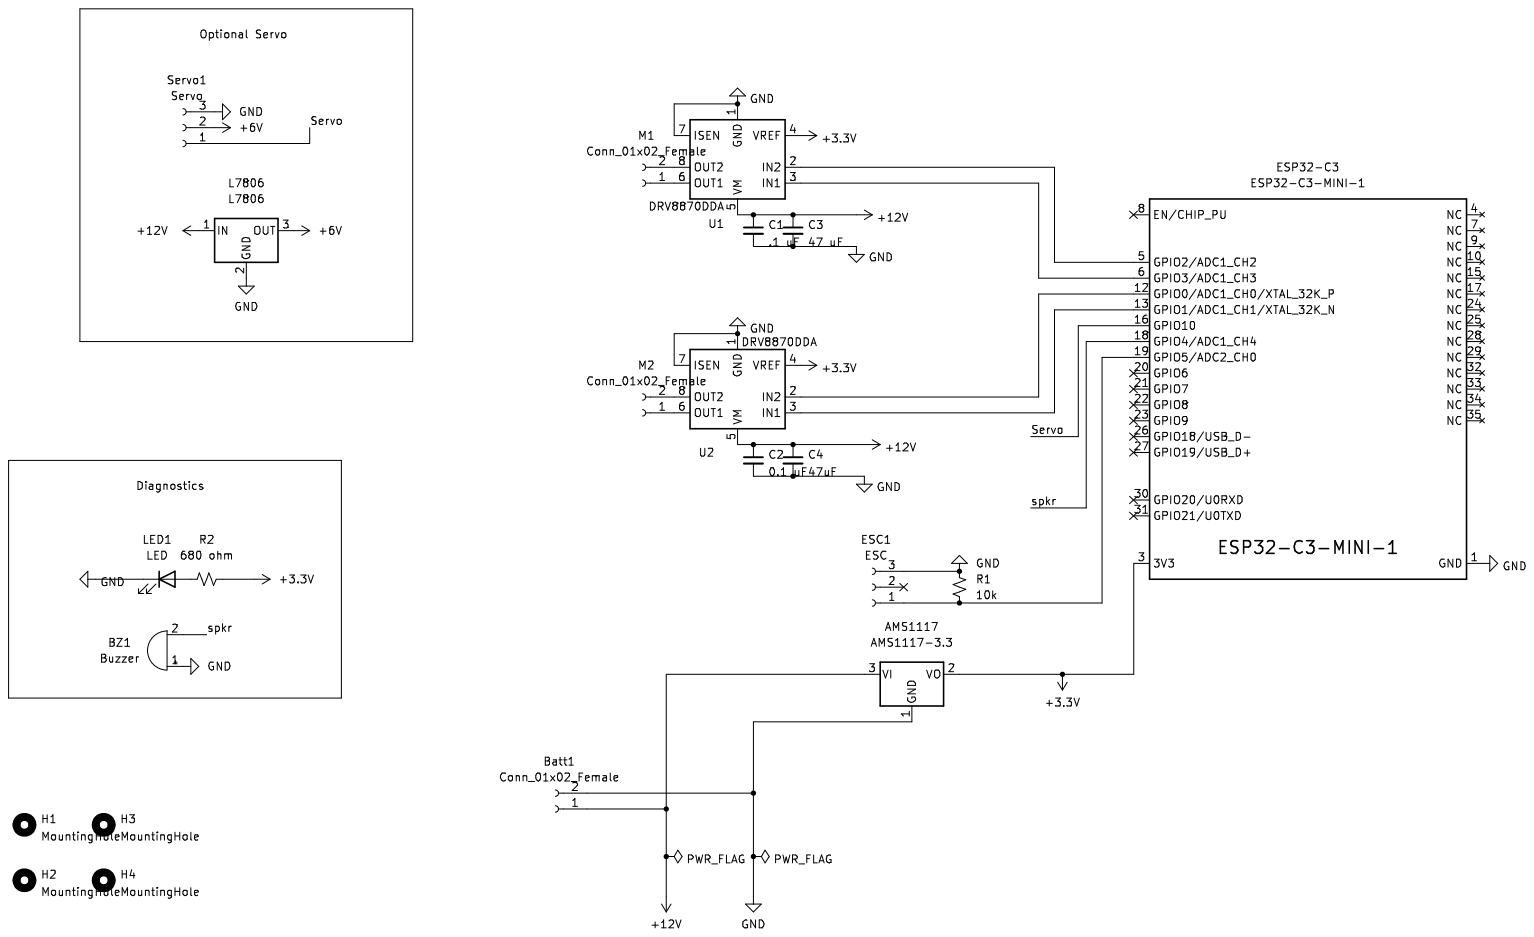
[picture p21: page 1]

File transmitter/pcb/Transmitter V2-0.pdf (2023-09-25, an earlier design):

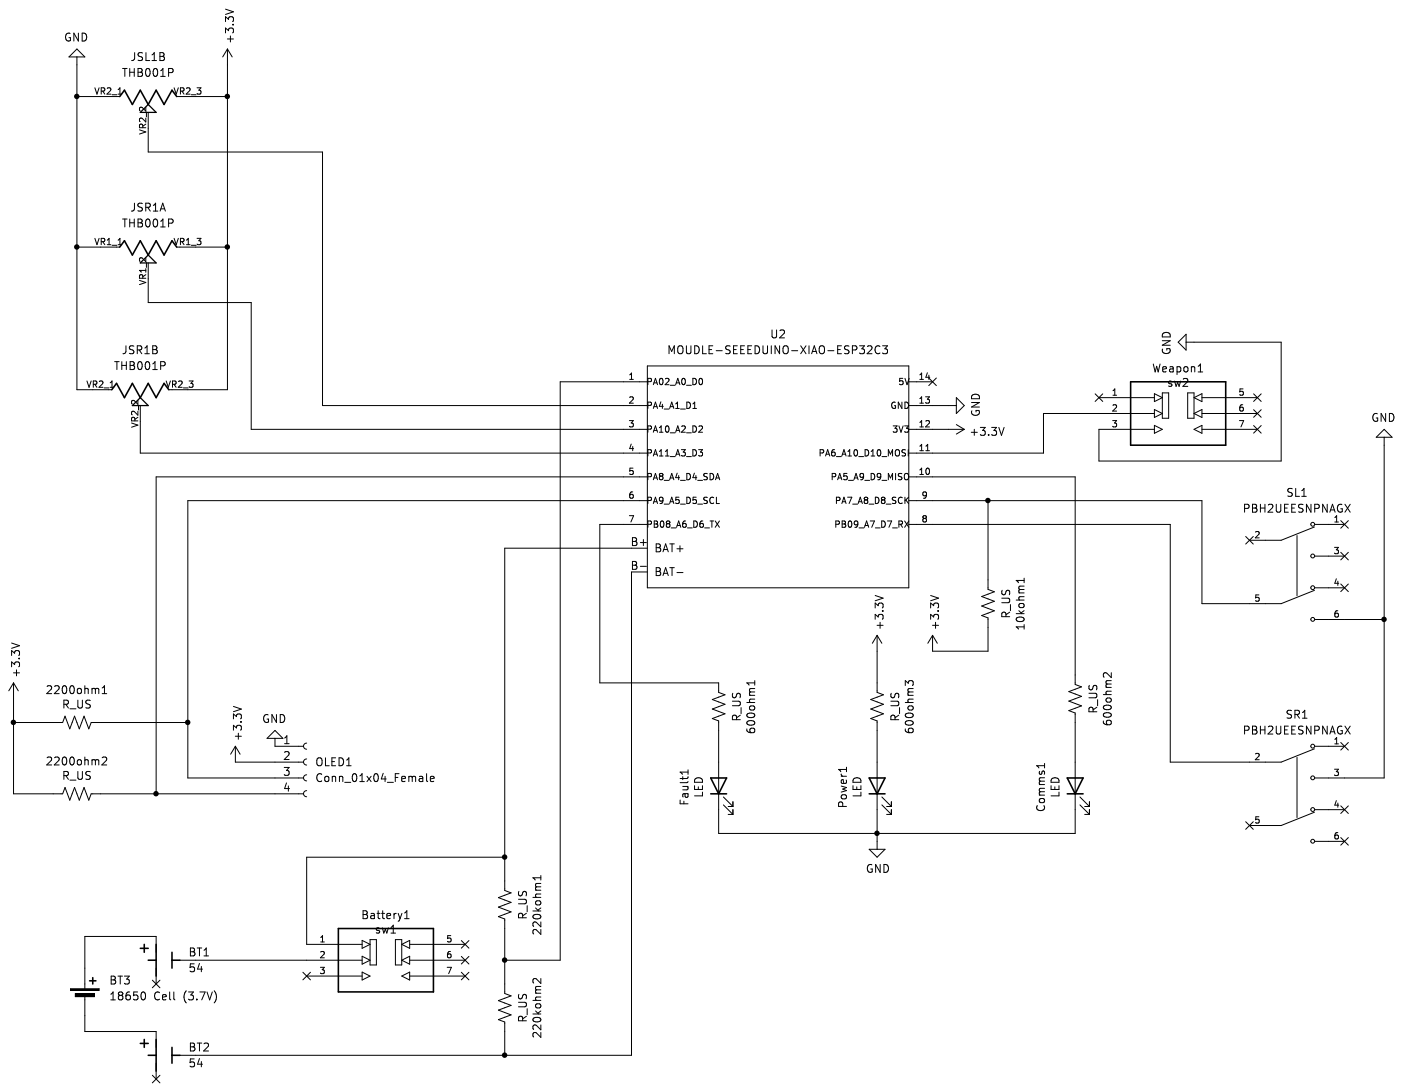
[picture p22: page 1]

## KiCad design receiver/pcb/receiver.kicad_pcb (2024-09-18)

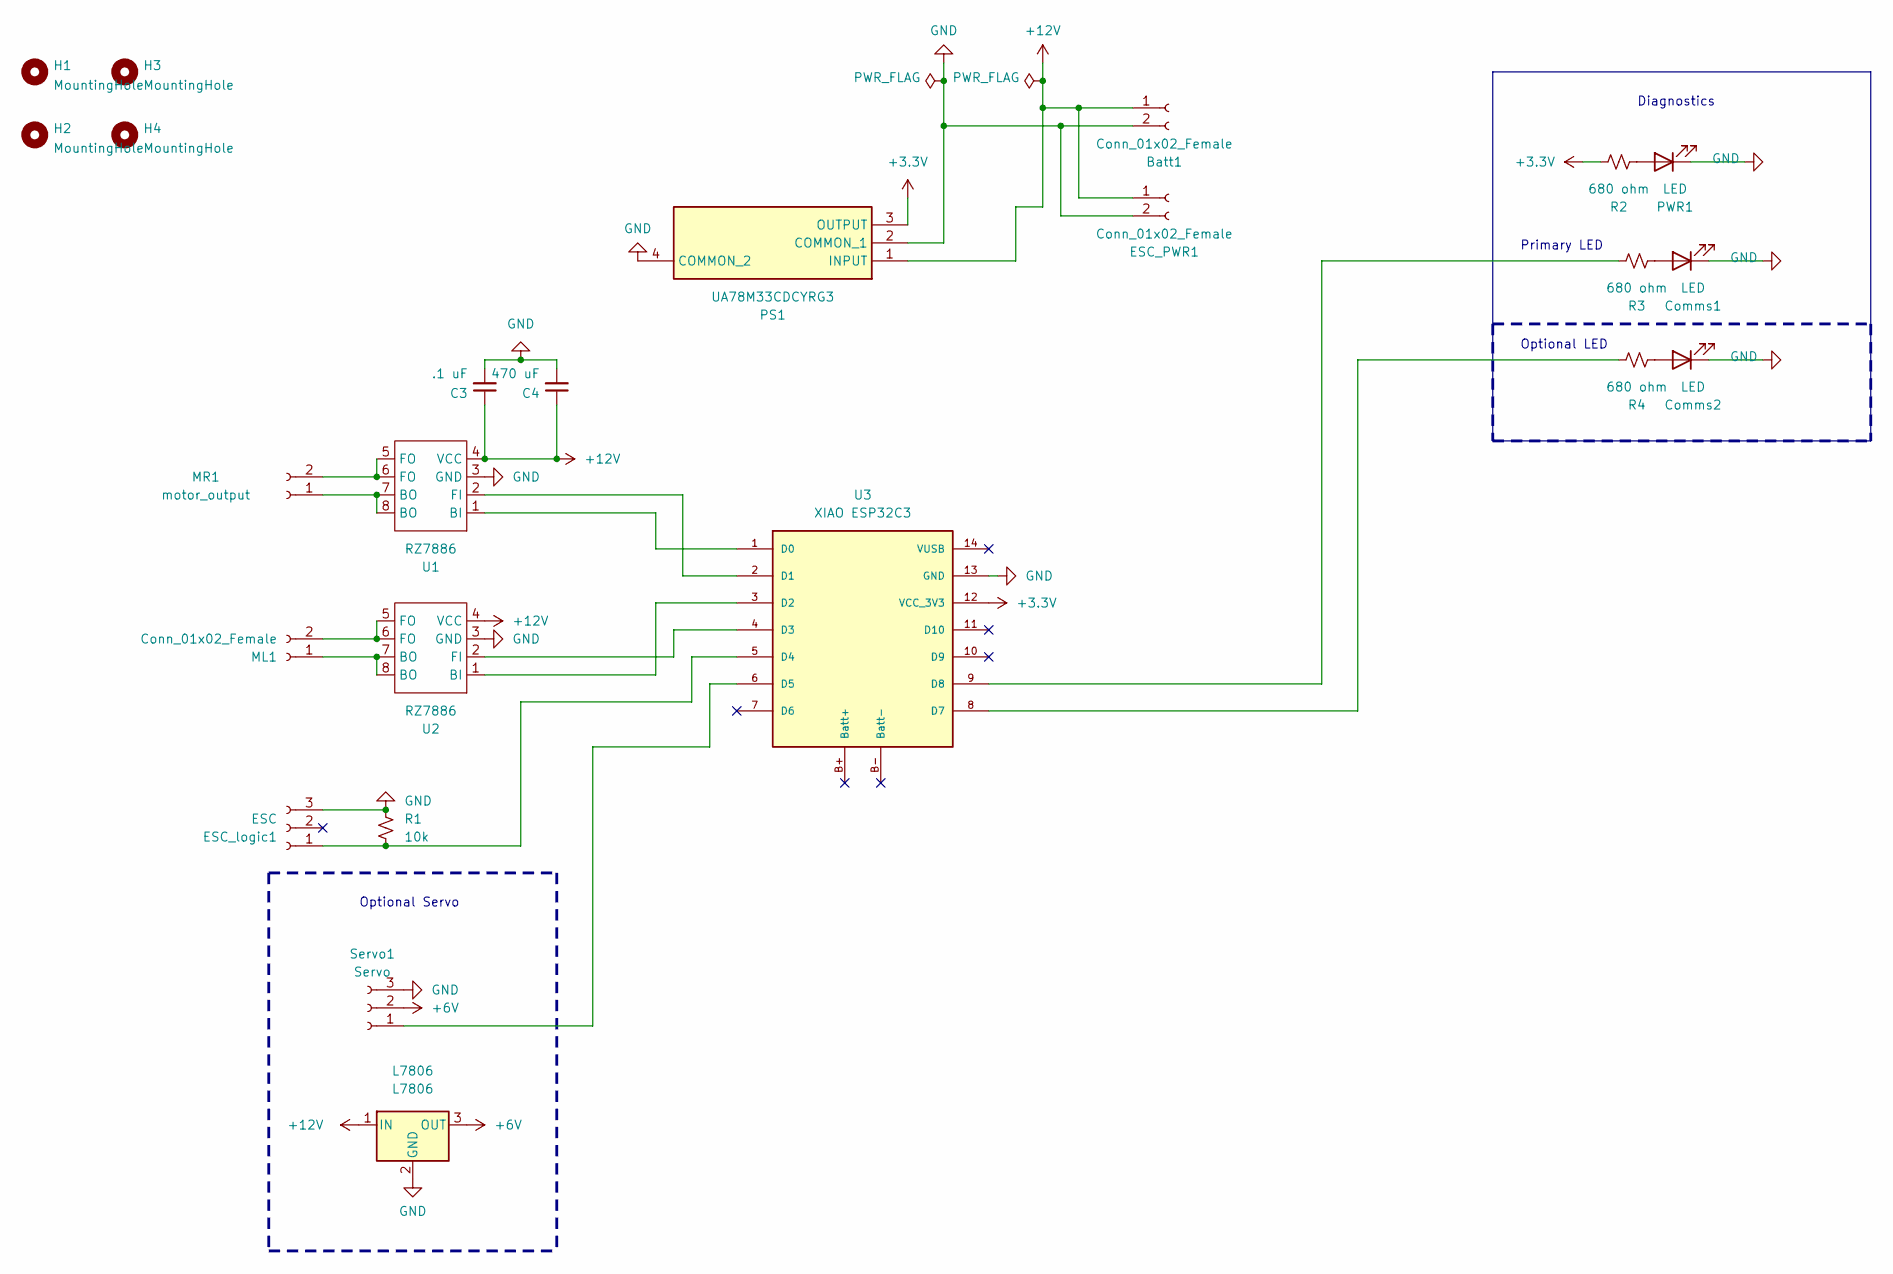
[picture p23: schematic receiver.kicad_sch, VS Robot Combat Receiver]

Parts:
Batt1: Conn_01x02_Female; battery_pads
C3: .1 uF; C_0805_2012Metric_Pad1.18x1.45mm_HandSolder
C4: 470 uF; CP_Radial_D8.0mm_P3.80mm
Comms1, Comms2: LED; LED_0805_2012Metric_Pad1.15x1.40mm_HandSolder
ESC_PWR1: Conn_01x02_Female; battery_pads
ESC_logic1: ESC; PinSocket_1x03_P2.54mm_Vertical
H1, H2, H3, H4: MountingHole; MountingHole_3.2mm_M3
L7806: L7806; TO-263-2_TabPin1
ML1: Conn_01x02_Female; PinSocket_1x02_P2.54mm_Vertical
MR1: motor_output; DC_motor_output
PS1: UA78M33CDCYRG3; SOT230P700X180-4N; Mouser Part Number 595-UA78M33CDCYRG3
PWR1: LED; LED_0805_2012Metric_Pad1.15x1.40mm_HandSolder
R1: 10k; R_0805_2012Metric_Pad1.20x1.40mm_HandSolder
R2, R3, R4: 680 ohm; R_0805_2012Metric_Pad1.20x1.40mm_HandSolder
Servo1: Servo; PinSocket_1x03_P2.54mm_Vertical
U1, U2: RZ7886; DIP-8_W7.62mm
U3: XIAO ESP32C3; xiao_esp32c3

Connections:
+3V3: PS1.3 (OUTPUT), R2.1, U3.12 (VCC_3V3)
+6V: L7806.3 (OUT), Servo1.2
+12V: Batt1.1, C3.1, C4.1, ESC_PWR1.1, L7806.1 (IN), PS1.1 (INPUT), U1.4 (VCC), U2.4 (VCC)
GND: Batt1.2, C3.2, C4.2, Comms1.1 (K), Comms2.1 (K), ESC_PWR1.2, ESC_logic1.3, L7806.2 (GND), PS1.2 (COMMON_1), PS1.4 (COMMON_2), PWR1.1 (K), R1.1, Servo1.3, U1.3 (GND), U2.3 (GND), U3.13 (GND)
unnamed: Comms1.2 (A), R3.2
unnamed: Comms2.2 (A), R4.2
unnamed: ESC_logic1.1, R1.2, U3.5 (D4)
unnamed: ML1.1, U2.7 (BO), U2.8 (BO)
unnamed: ML1.2, U2.5 (FO), U2.6 (FO)
unnamed: MR1.1, U1.7 (BO), U1.8 (BO)
unnamed: MR1.2, U1.5 (FO), U1.6 (FO)
unnamed: PWR1.2 (A), R2.2
unnamed: Servo1.1, U3.6 (D5)
unnamed: U1.1 (BI), U3.1 (D0)
unnamed: U1.2 (FI), U3.2 (D1)
unnamed: U2.1 (BI), U3.3 (D2)
unnamed: U2.2 (FI), U3.4 (D3)
unnamed: R4.1, U3.8 (D7)
unnamed: R3.1, U3.9 (D8)

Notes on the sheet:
Optional Servo
Diagnostics
Optional LED
Primary LED

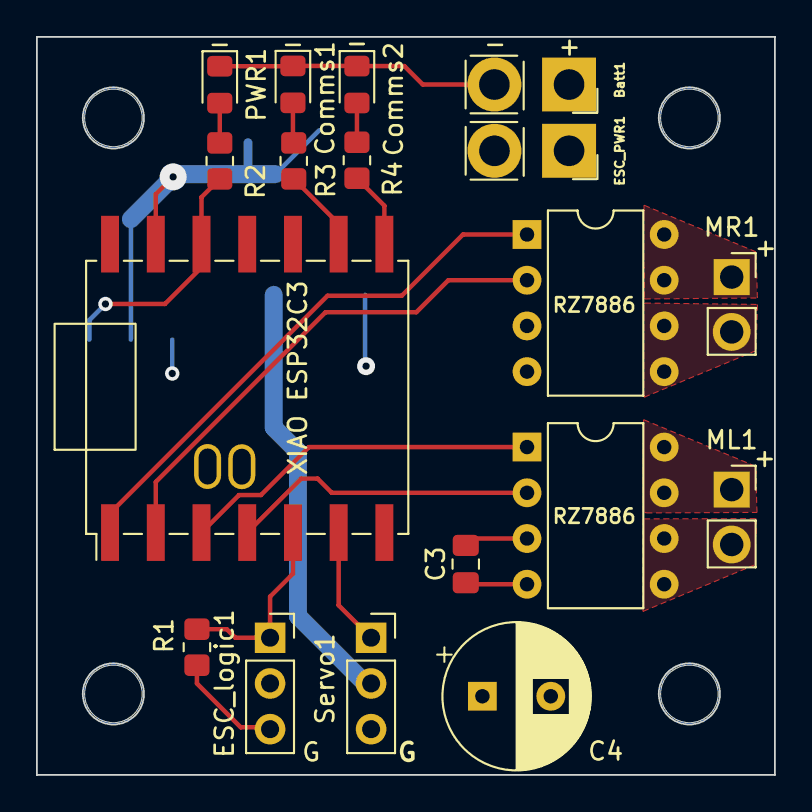
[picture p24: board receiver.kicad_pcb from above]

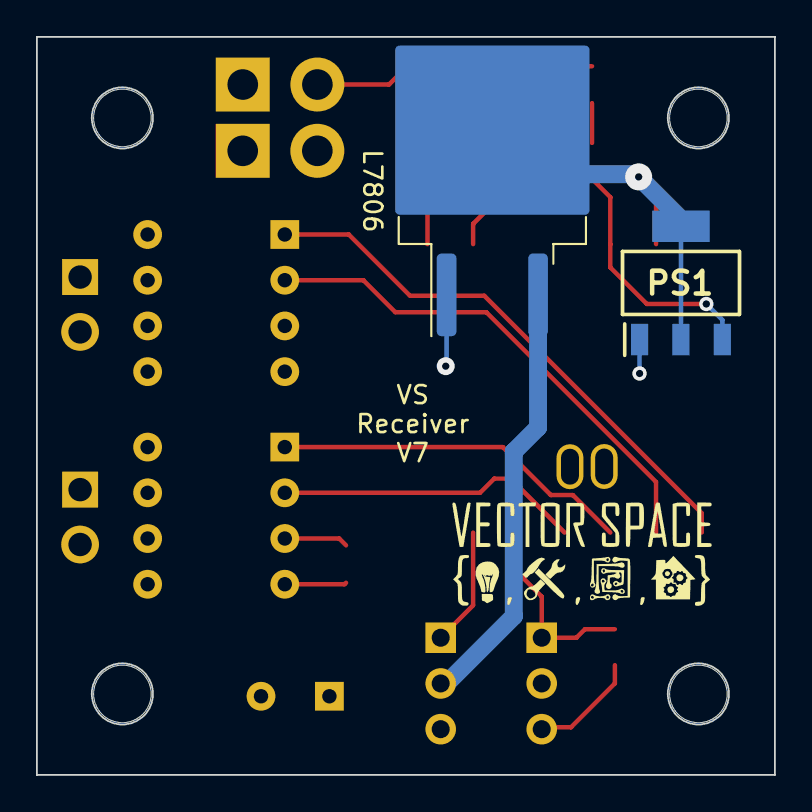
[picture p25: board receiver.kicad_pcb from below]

Board: 4 copper layers, 41.0 x 41.0 mm, 24 parts (2 on the bottom side), 19 nets.

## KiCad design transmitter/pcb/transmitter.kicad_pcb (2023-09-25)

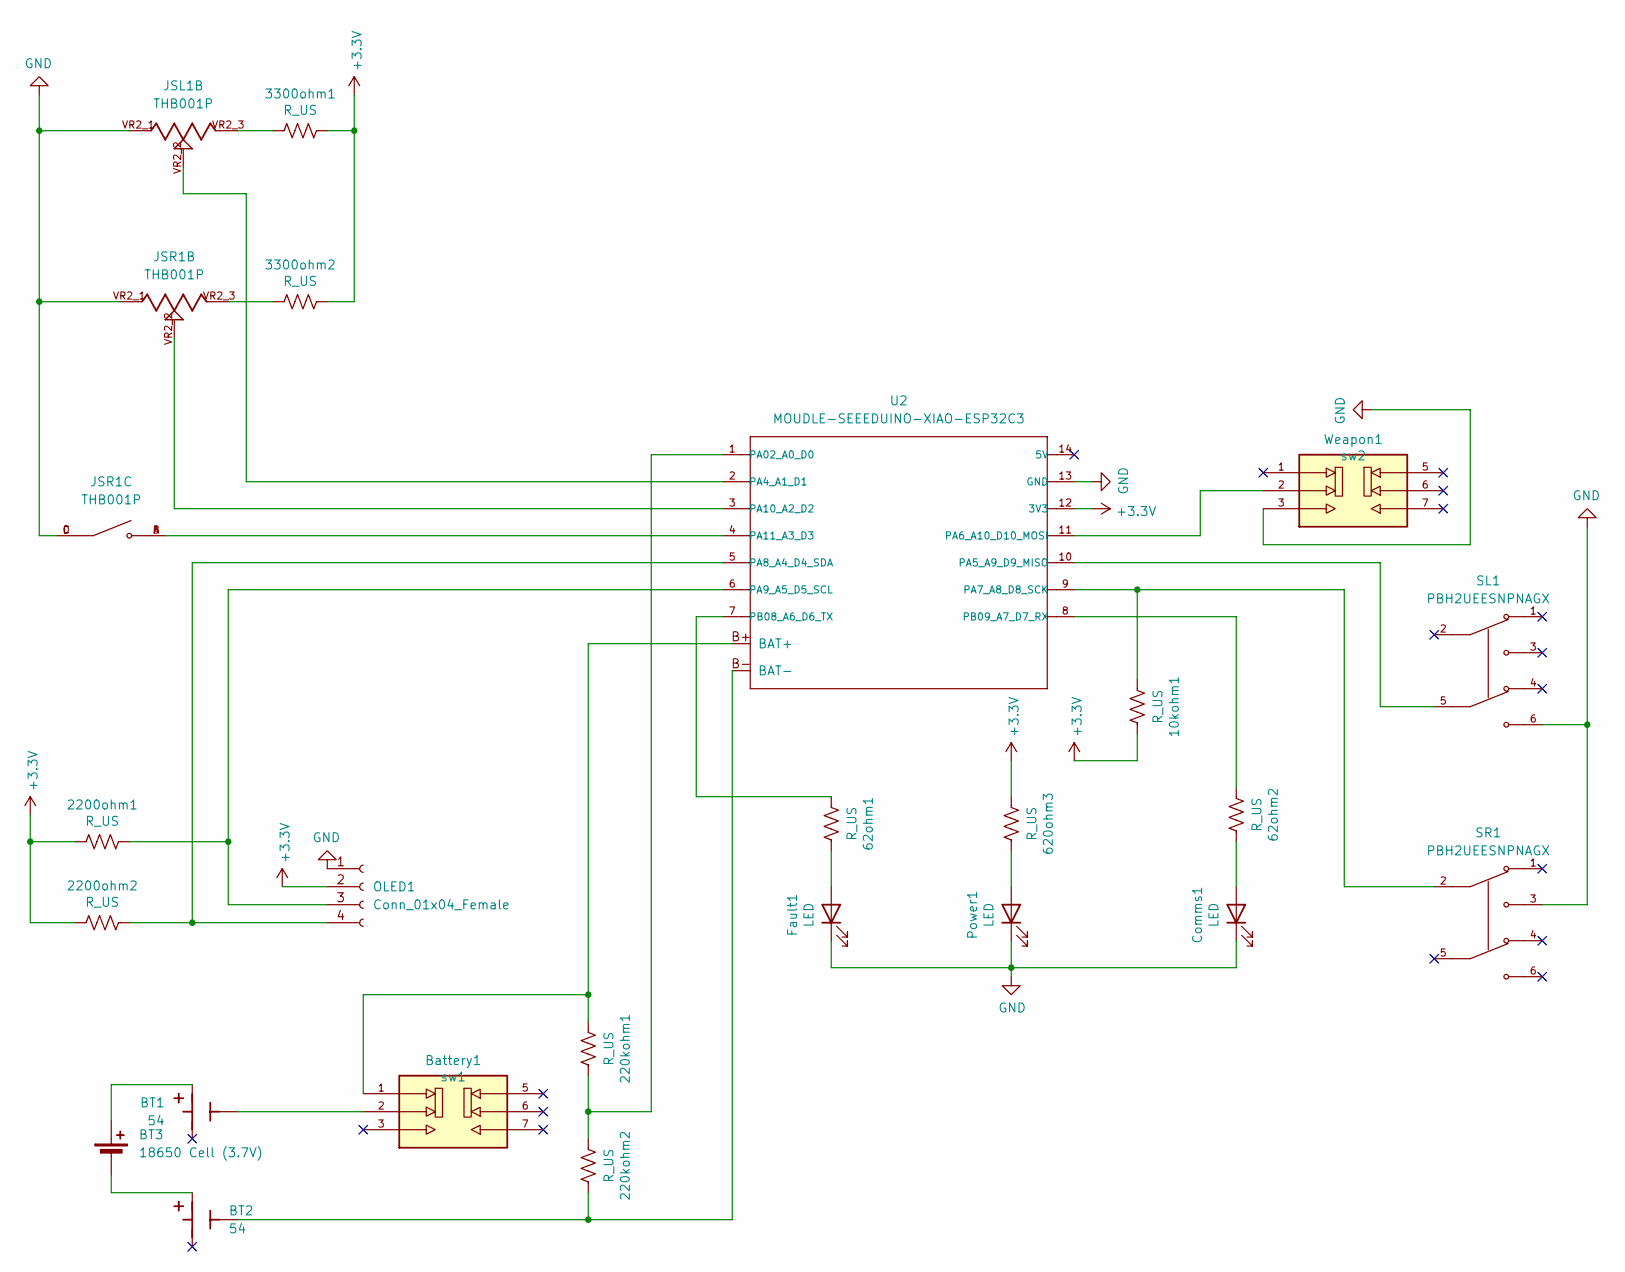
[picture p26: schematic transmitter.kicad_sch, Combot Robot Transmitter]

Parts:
10kohm1, 62ohm1, 62ohm2, 220kohm1, 220kohm2, 620ohm3, 2200ohm1, 2200ohm2, 3300ohm1, 3300ohm2: R_US; R_0805_2012Metric_Pad1.20x1.40mm_HandSolder
BT1, BT2: 54; BAT_54; PARTREV E
BT3: 18650 Cell (3.7V)
Battery1: sw1; SW_JS202011JCQN; PARTREV 11 Nov 19
Comms1: LED; LED_0805_2012Metric_Pad1.15x1.40mm_HandSolder
Fault1: LED; LED_0805_2012Metric_Pad1.15x1.40mm_HandSolder
JSL1: THB001P; CNK_THB001P; PARTREV 27 Jan 22
JSR1: THB001P; CNK_THB001P; PARTREV 27 Jan 22
OLED1: Conn_01x04_Female; PinSocket_1x04_P2.54mm_Vertical
Power1: LED; LED_0805_2012Metric_Pad1.15x1.40mm_HandSolder
SL1: PBH2UEESNPNAGX; SW_PBH2UEESNPNAGX; PARTREV E
SR1: PBH2UEESNPNAGX; SW_PBH2UEESNPNAGX; PARTREV E
U2: MOUDLE-SEEEDUINO-XIAO-ESP32C3; MOUDLE14P-SMD-2.54-21X17.8MM
Weapon1: sw2; SW_JS202011JCQN; PARTREV 11 Nov 19

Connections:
+3.3V: 10kohm1.1, 620ohm3.2, 2200ohm1.2, 2200ohm2.2, 3300ohm1.1, 3300ohm2.1, OLED1.2, U2.12 (3V3)
GND: Comms1.1 (K), Fault1.1 (K), JSL1.VR2_1, JSR1.C, JSR1.D, JSR1.VR2_1, OLED1.1, Power1.1 (K), SL1.6, SR1.3, U2.13 (GND), Weapon1.3
unnamed: 3300ohm1.2, JSL1.VR2_3
unnamed: 3300ohm2.2, JSR1.VR2_3
unnamed: BT1.1_3, Battery1.2
unnamed: BT1.1_1, BT3.1 (+)
unnamed: BT2.1_1, BT3.2 (-)
unnamed: 62ohm2.1, Comms1.2 (A)
unnamed: 62ohm1.1, Fault1.2 (A)
unnamed: 2200ohm1.1, OLED1.3, U2.6 (PA9_A5_D5_SCL)
unnamed: 2200ohm2.1, OLED1.4, U2.5 (PA8_A4_D4_SDA)
unnamed: 620ohm3.1, Power1.2 (A)
unnamed: 220kohm1.2, Battery1.1, U2.B+ (BAT+)
unnamed: 220kohm2.1, BT2.1_3, U2.B- (BAT-)
unnamed: 220kohm1.1, 220kohm2.2, U2.1 (PA02_A0_D0)
unnamed: JSL1.VR2_2, U2.2 (PA4_A1_D1)
unnamed: SL1.5, U2.10 (PA5_A9_D9_MISO)
unnamed: U2.11 (PA6_A10_D10_MOSI), Weapon1.2
unnamed: 10kohm1.2, SR1.2, U2.9 (PA7_A8_D8_SCK)
unnamed: JSR1.VR2_2, U2.3 (PA10_A2_D2)
unnamed: JSR1.A, JSR1.B, U2.4 (PA11_A3_D3)
unnamed: 62ohm1.2, U2.7 (PB08_A6_D6_TX)
unnamed: 62ohm2.2, U2.8 (PB09_A7_D7_RX)

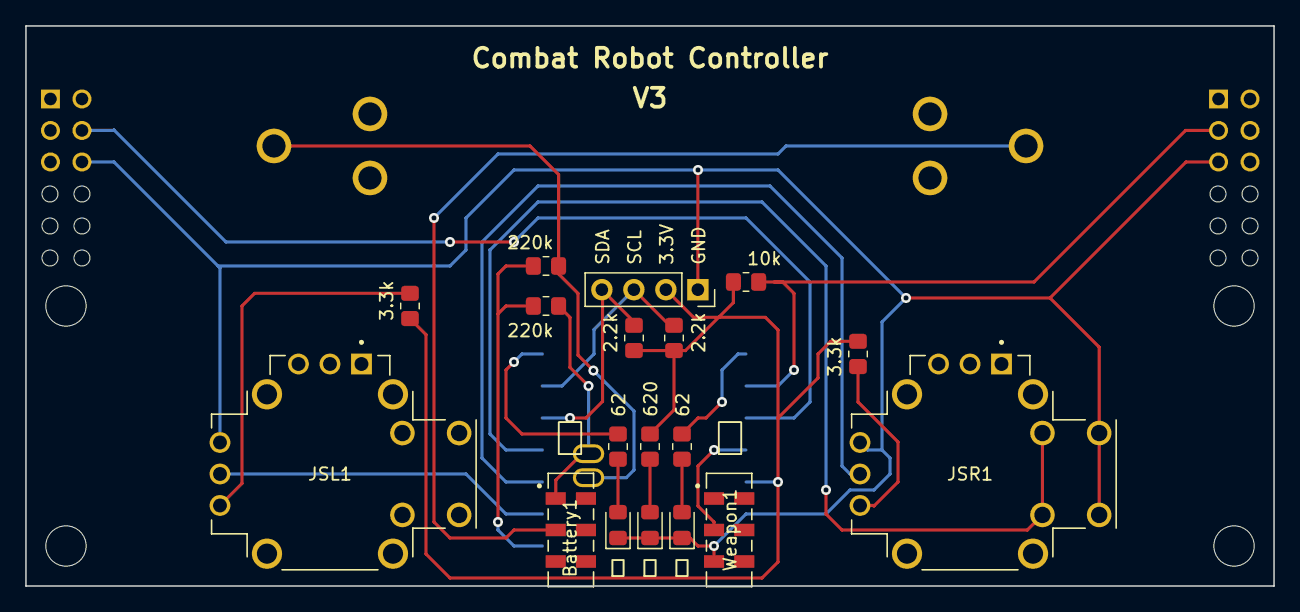
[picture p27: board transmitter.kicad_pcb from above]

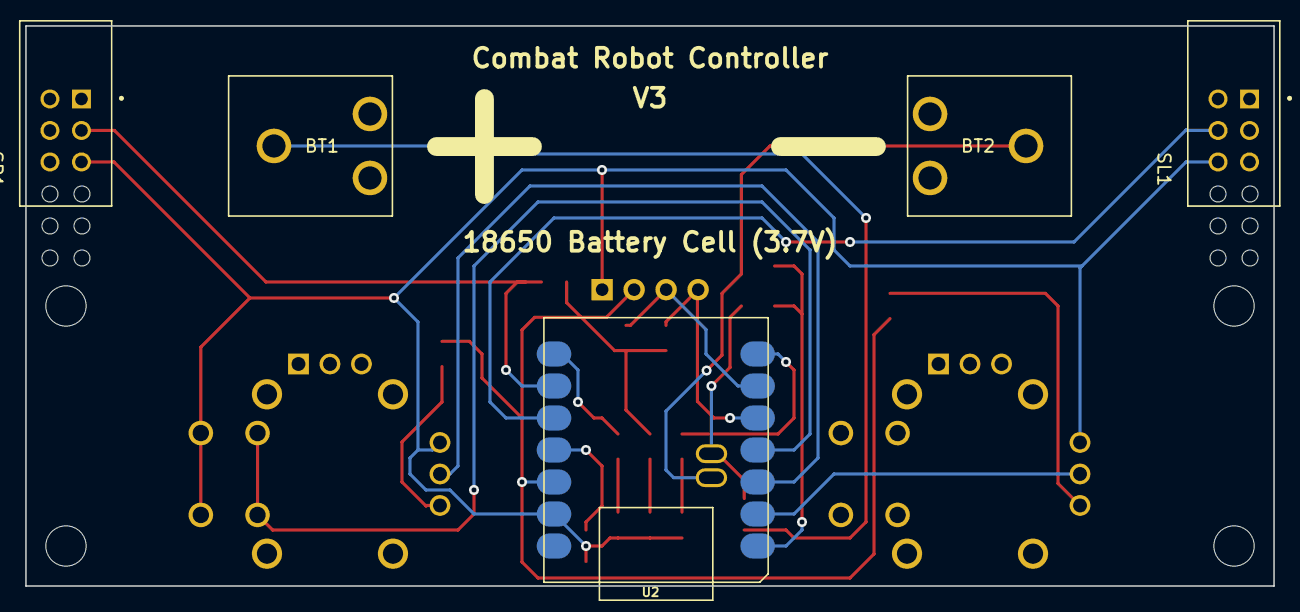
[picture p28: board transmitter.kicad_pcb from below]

Board: 2 copper layers, 99.1 x 44.5 mm, 23 parts (5 on the bottom side), 21 nets.

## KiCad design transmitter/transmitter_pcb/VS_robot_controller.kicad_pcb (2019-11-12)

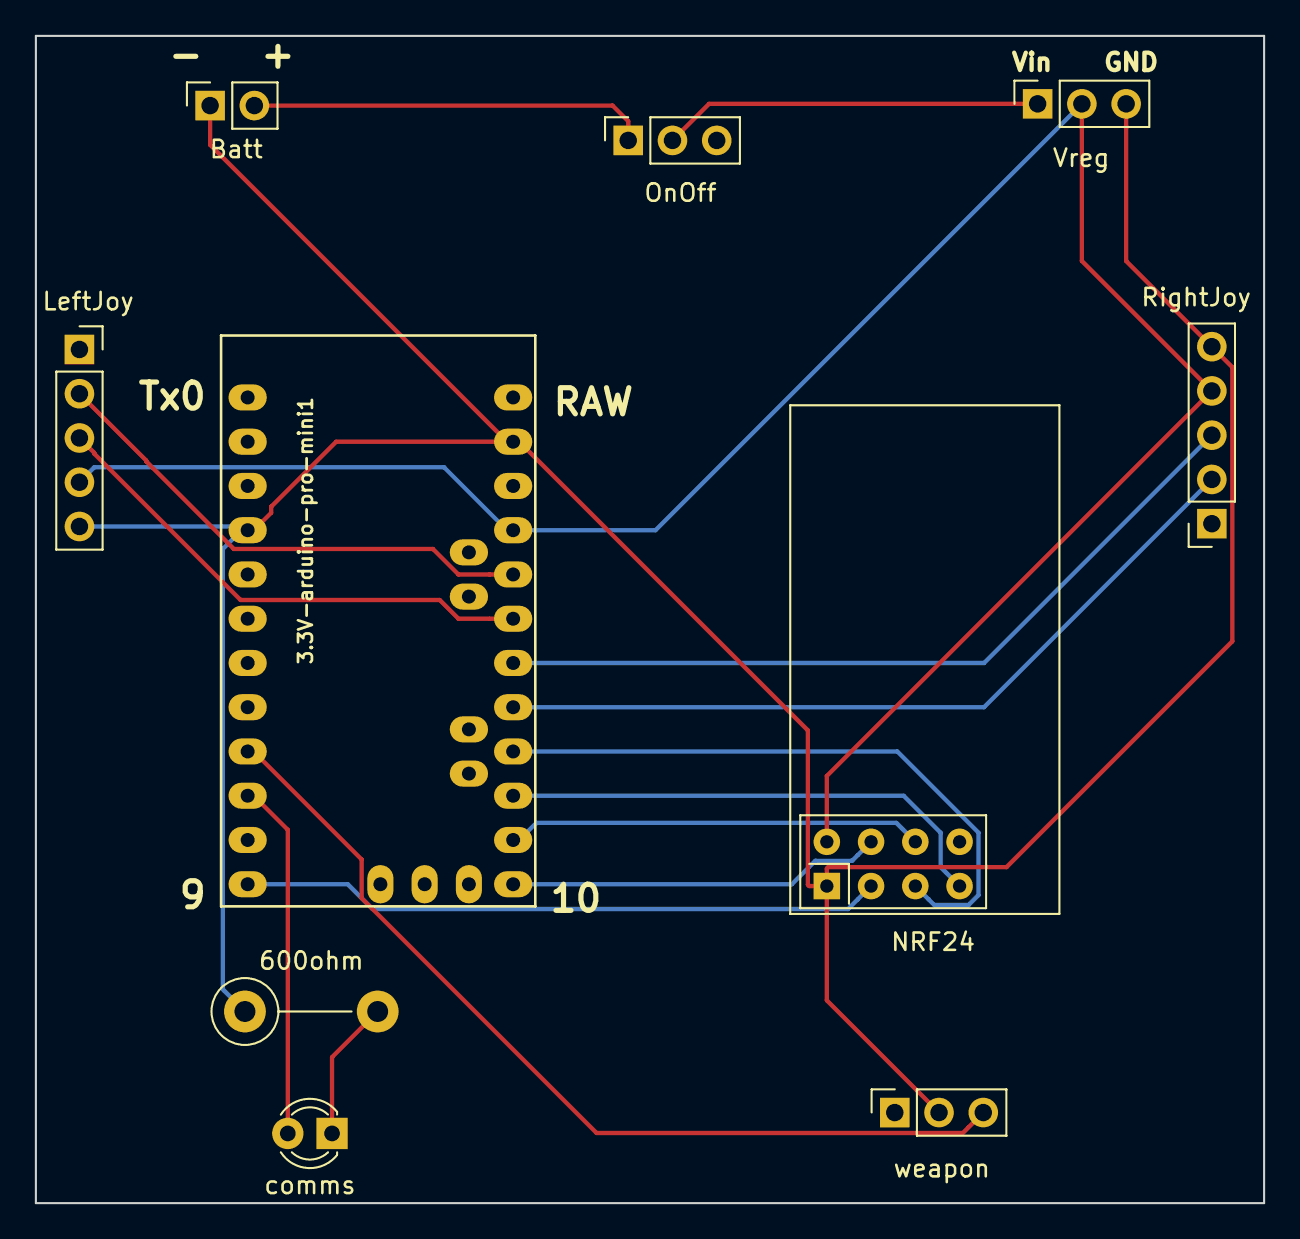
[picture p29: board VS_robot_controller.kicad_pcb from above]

Board: 2 copper layers, 70.5 x 67.0 mm, 10 parts (0 on the bottom side), 15 nets.

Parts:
3.3V-arduino-pro-mini1: arduino-pro-mini; pro_mini
600ohm: R_US; R_Axial_DIN0411_L9.9mm_D3.6mm_P7.62mm_Vertical
Batt: j2; PinSocket_1x02_P2.54mm_Vertical
LeftJoy: J3; PinSocket_1x05_P2.54mm_Vertical
NRF24: NRF24L01_Breakout; nRF24L01_Breakout
OnOff: sw1; PinSocket_1x03_P2.54mm_Vertical
RightJoy: J4; PinSocket_1x05_P2.54mm_Vertical
Vreg: j3; PinSocket_1x03_P2.54mm_Vertical
comms: LED; LED_D3.0mm
weapon: sw2; PinSocket_1x03_P2.54mm_Vertical

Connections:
+3V3: 3.3V-arduino-pro-mini1.21, LeftJoy.4, NRF24.2, RightJoy.4, Vreg.2
+12V: Batt.2, OnOff.1, OnOff.2, Vreg.1
GND: 3.3V-arduino-pro-mini1.4, 3.3V-arduino-pro-mini1.23, 600ohm.1, Batt.1, LeftJoy.5, NRF24.1, RightJoy.5, Vreg.3, weapon.2
unnamed: 3.3V-arduino-pro-mini1.9, weapon.3
unnamed: 3.3V-arduino-pro-mini1.10, comms.2
unnamed: 3.3V-arduino-pro-mini1.12, NRF24.3
unnamed: 3.3V-arduino-pro-mini1.13, NRF24.4
unnamed: 3.3V-arduino-pro-mini1.14, NRF24.6
unnamed: 3.3V-arduino-pro-mini1.15, NRF24.7
unnamed: 3.3V-arduino-pro-mini1.16, NRF24.5
unnamed: 3.3V-arduino-pro-mini1.17, RightJoy.2
unnamed: 3.3V-arduino-pro-mini1.18, RightJoy.3
unnamed: 3.3V-arduino-pro-mini1.19, LeftJoy.3
unnamed: 3.3V-arduino-pro-mini1.20, LeftJoy.2
unnamed: 600ohm.2, comms.1

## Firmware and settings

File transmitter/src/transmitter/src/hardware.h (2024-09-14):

#ifndef HARDWARE_H
#define HARDWARE_H

#define PIN_LEFT_JOYSTICK A1
#define PIN_RIGHT_JOYSTICK A2
#define PIN_LEFT_TRIGGER D9
#define PIN_RIGHT_TRIGGER D8
#define PIN_RIGHT_THUMB_SWITCH D3
#define PIN_WEAPON_TOGGLE_SWITCH D10
#define PIN_BATTERY_SENSE A0
#define PIN_FAULT_LED D6
#define PIN_COMMS_LED D7

#define DEFAULT_BATTERY_VOLTAGE_MULTIPLIER 2 //nominal 50/50 voltage divider on battery voltage sense
#define DEFAULT_BATTERY_LOW_RANGE_VOLTAGE 3.5
#define DEFAULT_BATTERY_HIGH_RANGE_VOLTAGE 4.25
#define DEFAULT_BATTERY_ALARM_LIMIT_VOLTAGE 3.75

#define DEFAULT_WIFI_LOW_SIGNAL -80
#define DEFAULT_WIFI_HIGH_SIGNAL -40


#define DEFAULT_WEAPON_SPEED 0x7FFF

#define DEFAULT_HORN_FREQUENCY 400


#endif

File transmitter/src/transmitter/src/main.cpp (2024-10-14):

#include <Wire.h>
#include <U8g2lib.h>
#include <esp_now.h>
#include <WiFi.h>
#include <nvs_flash.h>
#include <Preferences.h>
#include <SimpleCLI.h>
#include <PreferencesCLI.h>
#include "hardware.h"
#include "common.h"
#include "joystick.h"
#include "auto_pairing.h"
#include "diagnostics.h"
#include "UiUiUi.h" //DOWNLOAD FROM HERE BECAUSE IT HAS FIXES NOT IN ARDUINO VERSION: https://github.com/burksbuilds/UiUiUi
#include "UIStatusIndicator.h"
#include "UISidebar.h"
#include "UIDashboard.h"
#include "UIMessageBanner.h"
#include "wifi_comms.h"
#include "cli.h"
#include "auto_pairing.h"

#define SOFTWARE_VERSION "v2"

#define CONNECTION_TIMEOUT_MS 1000

//globals for transmitter states
TransmitterState currentState = TRANSMITTER_STATE_BOOT;
TransmitterFault currentFaults = TRANSMITTER_FAULT_NONE;
TransmitterWarning currentWarnings = TRANSMITTER_WARNING_NONE;

//globals for communication
//esp_now_peer_info_t receiverCommsInfo;
CommandMessage cmd_msg;          //outgoing
ResponseMessage rsp_msg;        //incoming

//globals for hardware
PairButton pairButton(PIN_LEFT_TRIGGER, PIN_RIGHT_TRIGGER, PIN_RIGHT_THUMB_SWITCH);
Joystick leftJoystick;
Joystick rightJoystick;
int16_t weaponSpeed = 0;


Diagnostics diagnostics;
LED faultLED(PIN_FAULT_LED);
LED commsLED(PIN_COMMS_LED);

uint16_t batteryStateOfCharge;
float batteryVoltage;
float batteryVoltageMultiplier;
float batteryVoltageLowRange;
float batteryVoltageHighRange;
float batteryVoltageAlarmLimit;

long restartTime;//if non zero, board will restart if millis() > restart 

//globals for screen
U8G2_SSD1306_128X64_NONAME_F_HW_I2C screen(U8G2_R2);
UISidebar robotSidebar = UISidebar(screen_icon_robot);
UIVerticalLine robotDivider = UIVerticalLine(&robotSidebar);

UIMessageBanner messageBanner = UIMessageBanner();
UIHorizontalLine messageBannerDivider = UIHorizontalLine(&messageBanner);
UIDashboard dashboard = UIDashboard(&messageBannerDivider);
UIRows centerArea = UIRows(&dashboard, &robotDivider);

UIVerticalLine controllerDivider = UIVerticalLine(&centerArea);
UISidebar controllerSidebar = UISidebar(screen_icon_controller, &controllerDivider);
UIColumns mainDivider = UIColumns(&controllerSidebar);
UIDisplay displayManager=UIDisplay(&mainDivider);




bool screenSetup(){
  screen.begin();
  displayManager.init(&screen);
  messageBanner.setMessage(UIStatusIcon::Info,"State Change","Entering Boot State");
  controllerSidebar.updateWifiStrength(-55);
  controllerSidebar.updateStatusIndicator(UIStatusIcon::Warning);
  controllerSidebar.updateBatteryLevel(0x7FFF);
  robotSidebar.updateWifiStrength(-65);
  robotSidebar.updateStatusIndicator(UIStatusIcon::Fault);
  robotSidebar.updateBatteryLevel(0xAFFF);
  return true;
}


void setup() {
  // TESTING -----
  commsLED.toggle();
  delay(1000);
  commsLED.toggle();
  delay(1000);
  // -------- -----

  currentState = TRANSMITTER_STATE_STARTUP;
  bool startupOK = true;

  Serial.begin(115200);
  Serial.println("Vector Space {Combat Robot}");
  Serial.println(SOFTWARE_VERSION);
  Serial.println("https://github.com/VectorSpaceHQ/VS_combat_robot\r\n");

  startupOK &= leftJoystick.setup(PIN_LEFT_JOYSTICK,"LeftJoystick", true);
  startupOK &= rightJoystick.setup(PIN_RIGHT_JOYSTICK,"RightJoystick", true);

  pinMode(PIN_WEAPON_TOGGLE_SWITCH,INPUT_PULLUP);
  pinMode(PIN_RIGHT_THUMB_SWITCH,INPUT_PULLUP);
  pinMode(PIN_RIGHT_TRIGGER,INPUT_PULLUP);
  pinMode(PIN_LEFT_TRIGGER,INPUT_PULLUP);
  pinMode(PIN_BATTERY_SENSE,INPUT_PULLUP);
  batteryVoltage = batteryVoltageMultiplier * (analogReadMilliVolts(PIN_BATTERY_SENSE) / 1000.0);

  /* pinMode(PIN_FAULT_LED,OUTPUT);
  digitalWrite(PIN_FAULT_LED,LOW);
  pinMode(PIN_COMMS_LED,OUTPUT);
  digitalWrite(PIN_COMMS_LED,LOW); */
  faultLED.off();
  commsLED.off();

  Preferences preferences;
  preferences.begin("Battery");
  batteryVoltageMultiplier = preferences.getFloat("Multiplier",DEFAULT_BATTERY_VOLTAGE_MULTIPLIER);
  batteryVoltageLowRange = preferences.getFloat("LowRange",DEFAULT_BATTERY_LOW_RANGE_VOLTAGE);
  batteryVoltageHighRange = preferences.getFloat("HighRange",DEFAULT_BATTERY_HIGH_RANGE_VOLTAGE);
  batteryVoltageAlarmLimit = preferences.getFloat("AlarmLimit",DEFAULT_BATTERY_ALARM_LIMIT_VOLTAGE);
  preferences.end();

  startupOK &= screenSetup();
  startupOK &= espNowSetup();
  startupOK &= cliSetup();
  startupOK &= diagnostics.setup();
  PairSetup();

  if(!startupOK)
  {
    currentState = TRANSMITTER_STATE_CRITICAL_FAULT;
    Serial.println("ERROR: Critical fault during startup is preventing transition to normal operation");
    faultLED.on();
    controllerSidebar.updateStatusIndicator(UIStatusIcon::Fault);
    messageBanner.setMessage(UIStatusIcon::Fault,"Critical Fault","Unable to complete startup");
  } else {
    currentState = TRANSMITTER_STATE_CONNECTING;
    Serial.println("Startup Successful, transitioning to connecting state");
    controllerSidebar.updateStatusIndicator(UIStatusIcon::None);
    messageBanner.setMessage(UIStatusIcon::Info,"Startup Complete","Connecting to robot...");
    faultLED.off();
  }


    Serial.println();
    Serial.print("> ");
}

void loop() {
  cmd_msg = GetCommandMessage();
  rsp_msg = GetResponseMessage();

  pairButton.loop(&commsLED);

  leftJoystick.loop();
  rightJoystick.loop();

  

  batteryVoltage = 0.99 * batteryVoltage + 0.01 * batteryVoltageMultiplier * (analogReadMilliVolts(PIN_BATTERY_SENSE) / 1000.0);
  batteryStateOfCharge = map(static_cast<uint16_t>(batteryVoltage*1000), batteryVoltageLowRange*1000, batteryVoltageHighRange*1000, 0, 0xFFFF);
  controllerSidebar.updateBatteryLevel(batteryStateOfCharge);

  if(currentState & (TRANSMITTER_STATE_OPERATION | TRANSMITTER_STATE_CONNECTING))
  {
    if(millis() - cmd_msg.send_time > 50){
        sendCommand(leftJoystick, rightJoystick, weaponSpeed);
    }

  }

  if(currentState == TRANSMITTER_STATE_OPERATION)
  {
    robotSidebar.updateStatusIndicator(UIStatusIcon::None);
    robotSidebar.updateWifiStrength(rsp_msg.wifi_strength);
    robotSidebar.updateBatteryLevel(256 * (uint16_t)rsp_msg.battery_charge);
    controllerSidebar.updateWifiStrength(0);//#TODO!
    //comms_led.on();
    if((millis() - rsp_msg.responseMessageTime) > CONNECTION_TIMEOUT_MS)
    {
      Serial.println("ERROR: Lost connection with receiver");
      currentState = TRANSMITTER_STATE_CONNECTING;
      robotSidebar.updateStatusIndicator(UIStatusIcon::Question);
      robotSidebar.updateWifiStrength(0);
      robotSidebar.updateBatteryLevel(0);
      messageBanner.setMessage(UIStatusIcon::Warning,"Robot Lost","Connection Lost");
      controllerSidebar.updateWifiStrength(0);
    }

    if(!digitalRead(PIN_RIGHT_TRIGGER))
    {
      weaponSpeed = DEFAULT_WEAPON_SPEED;
    }
    if(!digitalRead(PIN_LEFT_TRIGGER))
    {
      weaponSpeed = 0;
    }
  } else {
    weaponSpeed = 0;
  }

  if(currentState == TRANSMITTER_STATE_CONNECTING)
  {

    //comms_led.blink();
    if((millis() - rsp_msg.responseMessageTime) < CONNECTION_TIMEOUT_MS)
    {
      Serial.println("Receiver response received. Transitioning to operation state");
      currentState = TRANSMITTER_STATE_OPERATION;
      messageBanner.setMessage(UIStatusIcon::Info,"Robot Connected","Transmitter is Operating");
    }
  }

  if(restartTime > 0 && millis() > restartTime)
  {
    ESP.restart();
  }

  ParseCLI();

  dashboard.setValues(cmd_msg);
  displayManager.render(&screen);
  diagnostics.loop(currentState, &commsLED, &faultLED);

}

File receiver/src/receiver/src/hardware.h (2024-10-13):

#ifndef HARDWARE_H
#define HARDWARE_H
#include "Arduino.h"

#define PIN_LEFT_MOTOR_FORWARD 4 //D2
#define PIN_LEFT_MOTOR_BACKWARD 5 // D3
#define PIN_RIGHT_MOTOR_FORWARD 2 // D0
#define PIN_RIGHT_MOTOR_BACKWARD 3 // D1

#define PIN_PAIR_BUTTON D9

#define PWM_CHANNEL_LEFT_FORWARD 1
#define PWM_CHANNEL_LEFT_BACKWARD 2
#define PWM_CHANNEL_RIGHT_FORWARD 3
#define PWM_CHANNEL_RIGHT_BACKWARD 4

#define PIN_COMMS_LED D8
#define PIN_OPT_LED D7


#endif

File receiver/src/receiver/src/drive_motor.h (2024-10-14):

#ifndef DRIVE_MOTOR_H
#define DRIVE_MOTOR_H

#include "Arduino.h"
#include "driver/ledc.h"
#include "esp_err.h"

#define DEFAULT_DRIVE_PWM_FREQUENCY 100 //very high frequencies might blow up the RZ7886 driver chip. 5k is def bad, 1k is kinda bad.
#define DEFAULT_DRIVE_PWM_RESOLUTION LEDC_TIMER_8_BIT

class DriveMotor{
  public:
    DriveMotor();
    // bool setup(int forwardPin, int backwardPin, int forwardChannel, int backwardChannel,
    //            int pwmFrequency = DEFAULT_DRIVE_PWM_FREQUENCY,
    //            int pwmResolution = DEFAULT_DRIVE_PWM_RESOLUTION);
    bool init(int PinA, int PinB, 
               ledc_channel_t channelA, ledc_channel_t channelB);
    void loop(int speed, bool enable = true);
  private:
    bool _isSetup;
    ledc_channel_t _forwardChannel;
    ledc_channel_t _backwardChannel;
    ledc_timer_t _timer;
    int _maxCommand = (1<<DEFAULT_DRIVE_PWM_RESOLUTION) -1;
    int _lastSpeed = 0;
};

#endif

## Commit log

2019-11-12 initial commit.
    [VS_robot_controller-B_Cu.gbr, VS_robot_controller-B_Mask.gbr, VS_robot_controller-B_Paste.gbr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]
2019-11-12 Added README and modified LED label
    [VS_robot_controller-B_Cu.gbr, VS_robot_controller-B_Mask.gbr, VS_robot_controller-B_Paste.gbr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]
2019-11-12 joysticks were wired backwards. fixed
    [VS_robot_controller-B_Cu.gbr, VS_robot_controller-B_Mask.gbr, VS_robot_controller-B_Paste.gbr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]
2019-11-12 cleaned up silk screen labels, added polarity indication
    [VS_robot_controller-B_Cu.gbr, VS_robot_controller-B_Mask.gbr, VS_robot_controller-B_Paste.gbr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]
2019-11-12 moved joysticks up
    [VS_robot_controller-B_Cu.gbr, VS_robot_controller-B_Mask.gbr, VS_robot_controller-B_Paste.gbr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]
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2019-11-12 still organizing
    [VS_robot_controller.kicad_pcb, VS_robot_controller.sch]
2019-11-12 mixed up transmitter/receiver
    [VS_robot_controller.kicad_pcb, VS_robot_controller.sch]
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2020-07-07 added labels to the receiver outputs
    [VS_robot_receiver.kicad_pcb]
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2020-07-07 rewired the output pins for betting intuition and labeling
    [VS_robot_receiver.kicad_pcb]
2020-07-08 added logo on receiver board
    [VS_robot_receiver-B_Cu.gbr, VS_robot_receiver-B_Mask.gbr, VS_robot_receiver-B_Paste.gbr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]
2020-07-08 change 5v label to Vin
    [VS_robot_receiver.kicad_pcb]
2020-07-08 changed receiver pin labeling
    [VS_robot_receiver.kicad_pcb]
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2020-07-13 added pulldown resistors to output lines to prevent spurious motor action at startup
    [VS_robot_receiver.sch]
2022-04-07 flipped transmitter on/off switch
    [VS_robot_controller.kicad_pcb, VS_robot_receiver.sch, controller.fcstd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]
2022-06-13 set radio power to max. Major performance boost
    [VS_robot_receiver.sch]
2022-06-21 V1.3 of Receiver and 1.2 of Transmitter. These versions were ordered 6/21/22
    [VS_robot_controller-B_Cu.gbr, VS_robot_controller-B_Mask.gbr, VS_robot_controller-B_Paste.gbr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]
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2022-07-18 added wheel hub freecad model
    [wheel_hub.FCStd]
2022-07-18 tweaked wheel hub after test prints
    [VS_robot_receiver-B_Cu.gbr, VS_robot_receiver-B_Mask.gbr, VS_robot_receiver-B_Paste.gbr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]
2022-11-20 Rev 0 of ESP32-C3 receiver. This version sent for production
    [receiver_esp-drv.kicad_pcb, receiver_esp-drv.kicad_sch]
2022-12-03 initial commit of esp32 source code. Proof of concept
    [receiver_esp-drv.kicad_pcb, receiver_esp-drv.kicad_sch]
2022-12-03 added Isaac's robot design
    [Isaac_combat_robot.FCStd]
2022-12-03 minor controller design mod
    [controller.fcstd]
2022-12-03 added hbridge pads to Isaac_robot cad
    [Isaac_combat_robot.FCStd]
2022-12-09 adding drv pcb files
    [receiver_esp-drv.kicad_pcb, receiver_esp-drv.kicad_sch]
2023-07-30 changes to chassis design
    [Isaac_combat_robot.FCStd]
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2023-08-02 increase trace width on receiver pcb
    [receiver_esp-drv.kicad_pcb, receiver_esp-drv.kicad_sch]
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2023-08-02 removing unnecessary transmitter files
    [transmitter.sch]
2023-08-02 fixing receiver kicad files
2023-08-02 added 9v battery holder footprint and symbol
    [transmitter.kicad_pcb, transmitter.kicad_sch]
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2023-08-05 minor silkscreen mod on receiver
    [receiver.kicad_pcb]
2023-08-06 Ready for Review
    added trigger switches and joysticks
    schematic is probably fine, but all of the route tracing needs to be redone
    adjusted transmitter for ps4 geometry
    added footprints
    added passives adjusted pin assignment
    ready for review
    [54.step, JS202011JCQN.step, JS202011SCQN.step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]
2023-08-07 change ESC connection to 3pin header
    [receiver.kicad_pcb, receiver.kicad_sch]
2023-08-08 made square pin consistently more positive voltage
    [receiver.kicad_pcb, receiver.kicad_sch]
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2023-08-08 updates to robot chassis design. Ready for print
    [Isaac_combat_robot.FCStd]
2023-08-10 fixed mistaken subtraction of top cover mounting holes on chassis.
    [Isaac_combat_robot.FCStd]
2023-08-31 silkscreen updates after building rev1. Updates to motor test code and addition of buzzer test code
    [receiver.kicad_pcb]
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2023-09-06 adding receiver src files
    [Isaac_combat_robot.FCStd]
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2023-09-15 V3 transmitter PCB
    * moar resistor labels!
    * re-routed analog inputs for joysticks, swapped a joystick sideways input for joystick click
    * fixed improper use of a digital IO that needs to be an input
    * battery connections are a through-pad...very excited to see if this works!
    * spaced battery clips apart an extra 2.5mm
    * added extra resistance to bring joystick voltages back into 2.5V range
    * added some extra cutouts so we can use a 4 pole trigger button instead of 2 pole because its cheaper (momentary version)
    [transmitter.kicad_pcb, transmitter.kicad_sch]
2023-09-18 V3 of receiver as ordered.
    [receiver.kicad_pcb, receiver.kicad_sch]
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2023-09-29 added bill of materials
    [BoM.ods]
2023-09-29 fixed bug in buzzer and motor setup. Missing return value
    [drive_motor.cpp]
2023-09-29 fix buzzer test code
    [buzzer_test.ino]
2023-09-29 flip motor polarity for left motor
    [drive_motor.cpp, hardware.h]
2023-10-02 some debug printouts to resolve battery pwr issues
    [drive_motor.cpp, hardware.h, joystick.cpp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]
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2023-10-02 debugging weapon and left motor bug
    [drive_motor.cpp, hardware.h]
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2023-10-05 updated motor labels on receiver and added receiver schematic pdf
    [connection_plates.FCStd, receiver.kicad_pcb]
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2023-10-05 attempting to fix drive motor issue that shows conflict with brushless motor. Still not there.
    [drive_motor.cpp, drive_motor.h, drive_motor_experiment.ino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]
2023-10-06 receiver code works! both drive motors, buzzer, and brushless motor work independently and simultaneously. Code is still a mess and will be cleaned up next
    [brushless_motor_test.ino, buzzer_test.ino, drive_motor.cpp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]
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2023-10-09 Updated controller CAD
    added:
    * better clearance for left joystick
    * better clearance for screen header
    * holes to access reset/boot buttons
    [controller back.STL, controller handles.STL]
2023-10-09 added thumbstick cad model
    [thumbstick.3mf, thumbstick.FCStd]
2023-10-09 Added transmitter trigger button cad
    Left and Right versions are different. snap geometry is a total guess.
    [controller trigger button.SLDPRT, left trigger button.STL, right trigger button.STL]
2023-10-11 receiver code cleanup. Made weapon class more similar to drivemotor class. Async buzzer still isn't actually async
    [drive_motor.cpp, weapon.cpp]
2023-10-15 Transmitter Case Battery Clearance
    updated sldprt and STLs. 'handles' should be unchanged, but 'back' is new.
    [controller back.STL, controller handles.STL]
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2023-10-18 updates to arena and robot models
    [connection_plates.FCStd]
2023-10-19 Revised controller cad
    added more structure to a support rib
    [controller back.STL, controller handles.STL]
2023-10-20 fixed mistake in button_test.ino
    [button_test.ino]
2023-10-20 fixed weapon.cpp bug that obviously didn't compile.
    [weapon.cpp]
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2023-11-01 more bot progress and some renaming of countdown timer code
    [connection_plates.FCStd]
2023-11-01 Added power switch to case
    [ButtonCase-HoleSide.STL, ButtonCase.SLDASM, ButtonCase.SLDPRT]
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2023-11-02 add 3mf files for wheel
    [wheel_hub_casting-mold.3mf, wheel_hub_casting-wheel.3mf]
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2023-11-05 fix match duration
    updated from 20 second demo duration to 2 minute match duration.
    [clock.ino]
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2023-11-08 Button Case Magnets
    And exported a HoleSide with no reset button switch
    [ButtonCase-HoleSide-NoReset.STL, ButtonCase-HoleSide.STL, ButtonCase-SolidSide.STL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]
2023-11-08 ButtonCase: added hex nut grip to top
    [ButtonCase-HoleSide-NoReset.STL, ButtonCase-HoleSide.STL, ButtonCase-SolidSide.STL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]
2023-11-08 Final Software update
    set trigger pins
    updated clock time
    added "program didn't crash" led to trigger
    [clock.ino, remote.ino]
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2023-11-09 chassis changes to fit different motors
    [wheel_hub_casting-wheel.3mf]
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2023-11-26 added led diagnostic lights to receiver. Removed buzzer. Added prefscli
    [common.h]
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2024-07-01 removed buzzer from motor test and created simple led test
    [drive_motor_test.ino, led_test.ino]
2024-08-12 Receiver V5 as ordered.
    [Seeed Studio XIAO-ESP32-C3.step, receiver.kicad_pcb, receiver.kicad_sch]
2024-08-16 JLCPCB didn't like my gerber naming convention and couldn't figure out the layer order. Their recommended names are really far from what KiCAD produces, but I've at least changed the names now to be 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
    [receiver.kicad_pcb]
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2024-09-01 V6 receiver board as ordered. Rearranged things, improved symbols and footprints, bigger power traces, corrected L7806 footprint, additional diagnostic LED
    [Seeed Studio XIAO-ESP32-C3.step, receiver.kicad_pcb, receiver.kicad_sch]
2024-09-01 corrected receiver 3d model esp32c3 location
    [Seeed Studio XIAO-ESP32-C3.step, receiver.kicad_pcb]
2024-09-08 transmitter UI fixes
    fixed tons of small UI things:
    * throttle bars
    * battery bar
    * wifi icon
    * message block
    [hardware.h]
2024-09-14 removing separate platformio version of receiver code because that was a sloppy way to do things.
    [auto_pairing.cpp, cli.cpp, common.h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]
2024-09-18 fixed mistakenly small motor pads in receiver V6.
    [receiver.kicad_pcb, receiver.kicad_sch]
2024-09-18 fix receiver comms pin for V6
    [hardware.h, main.cpp]
2024-09-22 fixed bug in receiver where pairing routine would stop too soon if it already had the TX mac stored. It was stopping before sending the RX mac back to TX.
    [auto_pairing.cpp, main.cpp]
2024-09-22 beginning migration of transmitter code to platformio. Compiles but likely doesn't work.
    [common.h, main.cpp]
2024-09-22 moved command line stuff to cli.cpp. Knowingly broke restartCommand and getVariableCommandCallback. Need Andrew's help fixing without use of globals
    [cli.cpp, common.h, joystick.cpp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]
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2024-10-11 revised controller CAD
    * fixed screen mounting
    * added better thumbstick clearance
    * added thumbstick part
    * flattened back of case and added logo
    [controller back.STL, controller handles.STL, controller thumbstick.SLDPRT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]
2024-10-13 fixed drive motor direction, fixed weapon pin number, correct UiUiUi dependency.
    [hardware.h, main.cpp]
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2024-10-14 initial commit of beater bar design. It has been through several iterations already.
    [VS_beater_bot.FCStd]
2024-10-22 more progress on beater bot, almost ready for aluminum.
    [VS_beater_bot.FCStd, wheel_hub_casting.FCStd]
2024-10-25 quick fix for issue of multiple transmitters controlling single receiver.
    [VS_beater_bot.FCStd, wheel_hub_casting.FCStd]
